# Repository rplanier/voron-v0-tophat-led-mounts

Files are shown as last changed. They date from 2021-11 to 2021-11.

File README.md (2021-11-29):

# Voron V0.1 Tophat LED Mounts

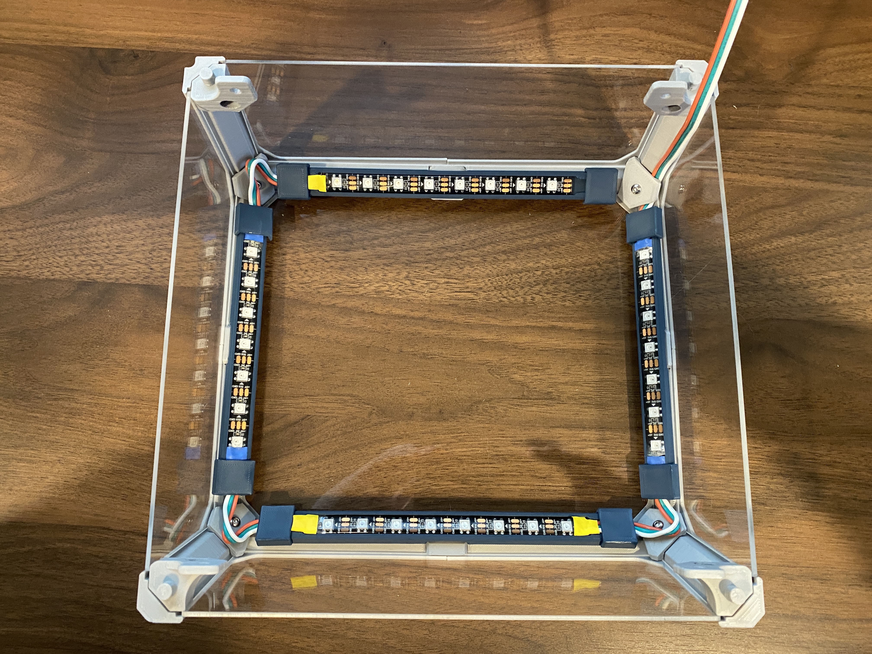
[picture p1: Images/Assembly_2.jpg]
Assembled Tophat


This mod for the Voron V0.1 adds four (4) LED mounting bars to the tophat and is designed to be minimumally intrusive and simple to build. It supports up to thirty (30) LEDs, which is the maximum officially supported using the BigTreeTech DCDC5V breakout power module. This guide assumes that you have a Voron V0.1 with a BigTreeTech SKR Mini E3 V2 controller board and the DCDC5V breakout power module (linked in the [BOM](#bill-of-materials) below.).

***Note:*** The LED mounting bars are too long to fit on a Voron V0 bed. However, the Fusion 360 CAD file has been included, and new mounting bars can easily be created by changing the user parameters.

## Table of Contents
- [Bill of Materials](#bill-of-materials)
- [Recommended Tools](#recommended-tools)
- [Printed Parts](#printed-parts)
- [Assembly Instructions](#assembly-instructions)
- [Klipper Configuration](#klipper-configuration)
- [Photos](#photos)
- [Contributors](#contributors)

## Bill of Materials

The following parts are required (unless otherwise denoted) to complete the assembly:

| Part | Quantity | Link | Notes |
| --- | :-: | --- | --- |
| BigTreeTech DCDC5V Power Module | 1 | https://www.biqu.equipment/products/bigtreetech-dcdc5v-v1-0-power-module-5v-for-skr-mini-e3-v1-2-skr-mini-e3-v3-0-32bit-control-board-rgb-light | Required to run up to 30 total LEDs, otherwise the SKR Mini E3 V2 only supports up to 8 LEDs. |
| WS2812B RGB IP65 5v LED Strip | 16.4 ft., 300 LEDs (OR) 3.2 f.t, 60 LEDs | https://amzn.to/3l4htHR | Channels in the mounting bars are designed to fit this exact 10mm-wide LED strip. Any LED strip you use should be 5 volts, 10mm wide, and approximately 16.5mm in length or less per LED diode. |
| 3-Pin 18 AWG PVC Copper Ribbon Wiring | 3+ ft. | https://amzn.to/3nSPr4d | 3-pin ribbon wiring is easier to work with for this mod, but any wiring will work. The reviews for the linked part suggest this wiring may actually be 20 AWG, but that is probably preferred anyway. |
| 1/4" Diameter Heat Shrink Tubing | 7 | https://amzn.to/3HMqvTM | Heat shrink tubing will protect the solder joints on the LED wiring pads (otherwise the pads may rip off during assembly). Cut 7 pieces to about 1/2" long each. |
| JST-XH 2.54mm 3-Pin Female Connector | 1 | https://amzn.to/30Vttoj | A JST-XH or similar 2.54mm connector is required to plug the LED strips into the Neopixel pins on the SKR Mini E3 V2 board. |
| Molex Micro-Fit 3.0 3-Pin Male/Female Connectors | 1 each | https://amzn.to/3FLt3zN | | **Optional**. To be added in-line within the printer chamber to allow for quick disconnects when removing the tophat for maintenance. |
| M3x10 Button Head Cap Screws | 8 | https://amzn.to/3HGdOd0 (OR) https://www.boltdepot.com/Product-Details.aspx?product=22819 | These will replace the 8x M3x6 screws used to bolt the tophat center clips to the tophat frame. |

## Recommended Tools

The following tools are recommended to complete the assembly:

| Tool | Link | Notes |
| --- | --- | --- |
| 3D Printer with >= 200mm Bed | | The largest part is about 185mm long, and you are encouraged to use a brim which further increases the length. ***No, the LED mounting bars will not fit on a Voron V0 bed.*** |
| Wire Strippers | https://amzn.to/3HNQ86u | For cutting and stripping wires between the LED strips. |
| Crimping Pliers | https://amzn.to/3cIcCry | For crimping JST-XH connector and other terminals. |
| Soldering Iron | https://amzn.to/3CNMZjv | You will need to solder 21 joints, plus maybe another 9 joints once you realize that once again you forgot to slide on the heat shrink tubing before soldering. |
| Tin Lead Rosin Core Solder Wire | https://amzn.to/30PILdR | |
| 2mm Hex Driver | | |

## Printed Parts

Each of the following parts should be printed in either ABS or ASA. ***Print each of the LED mounting bars with supports under the center of each bar where it will mount to the tophat center clip.***

| Part | Quantity | LED Angle | Supports Needed |
| --- | :-: | --- | --- |
| Front LED Bar | 1 | 15 degrees | Yes|
| Side LED Bar | 2 | 15 degrees | Yes |
| Back LED Bar | 1 | 5 degrees | Yes |
| End Clip | 8 | | No |

## Assembly Instructions

Reference the [photos](#photos) below during assembly for visual aid.

1. Print each of the [printed parts](#printed-parts). Test fit the end clips as described in Step 10 below.
2. Remove the existing M3x6 button head cap screws from the tophat center clips and install the front, back, and side LED mounting bars over the center clips using M3x10 button head cap screws. Each of the mounting bars is angled to better direct light toward the build plate. Ensure that the LED mounting bars are installed in the orientation that will direct light downward rather than upward.
3. Cut **2** strips of **7** LEDs for the front and back and **2** strips of **8** LEDs for the sides. I recommend leaving the full contact pad length on each end of a strip rather than cutting the contact pads in half. This means that for each 2 strips of LEDs you cut, you will throw away the LED diode between them because it won't have any contact pads. This will give you the greatest amount of surface area to ensure your soldering joints are strong.
4. Gently insert a seven **7**-LED strip and an **8**-LED strip into adjacent mounting bars to ensure that they will fit and measure the amount of 3-pin wire you will need between them. You will need somewhere around 3.5" of wire at each corner. Remove the strips from the mounting bars.
5. Cut off only the portion of IP65 protective plastic covering the contact pads on each end of the LED strips, except that you should not cut off the plastic covering the last set of contacts on the last LED strip since it will not be used. I have found the best way to do this is to peel away the covering from the LED strip by hand just enough to fully expose the contact pads and cut the covering with wire strippers.
6. Solder all the LED strips together with a strand of the measured 3-pin wire between each of them. ***Remember to add heat shrink tubing to your wires for each of your solder joints.***
7. Measure the length of wire needed to connect your first LED strip to the controller board and then cut and solder it to the first LED strip. If using a BigTreeTech SKR Mini E2 V2, crimp and add the JST-XH connector at the other end.
8. Slide the heat shrink tubing over the solder joints on each LED strip and apply heat to shrink them. Do not overheat or they will split and fall off.
9. Install each LED strip into its appropriate mounting bar by firmly pressing until it catches. You should not need to use the adhesive backing. Firmly press the wiring on each end of the LED strip into the mounting bar wiring channels.
10. Install the end clips on the ends of each mounting bar. The snap-fit connections are a bit oversized to ensure they strongly hold the wiring in place, so you may need to press firmly and/or twist the clips to install them properly.
11. Install the BigTreeTech DCDC5V power module onto the SKR Mini E3 V2 controller board. Be sure to move the appropriate jumper on the controller board to ensure it uses the power module rather than the on-board 5v controller for Neopixel/LED power (this is what allows you to use up to 30 LEDs rather than only 8). Consult the DCDC5V power module documentation for details.
12. Connect the JST-XH connector to the Neopixel port on the SKR Mini E3 V2.
13. Follow the [Klipper configuration](#klipper-configuration) instructions below for setting up the LEDs in the Klipper `printer.cfg` configuration file.

## Klipper Configuration

Add the following to `printer.cfg` in Klipper if using RGB LEDs:

```
###################################
# Neopixels / LEDs
###################################
[neopixel my_neopixel]
pin: PA8
chain_count: 30
color_order: GRB
initial_RED: 1
initial_GREEN: 1
initial_BLUE: 1
```

The LEDs can be changed by sending the command `SET_LED LED=my_neopixel RED={x} GREEN={x} BLUE={x}`, where `{x}` is a decimal value between 0 and 1. Consult the [Klipper documentation](https://www.klipper3d.org/Config_Reference.html#neopixel) for more information and configuration options.

## Photos

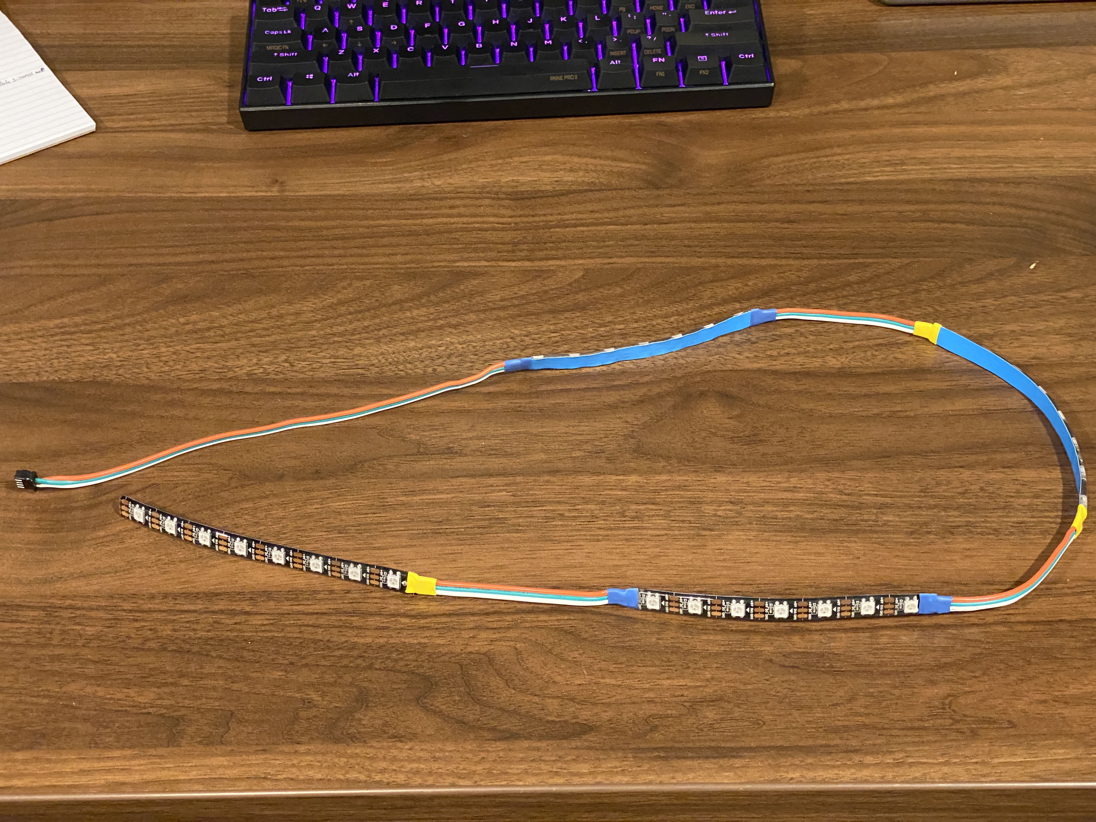
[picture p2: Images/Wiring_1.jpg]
Wiring 1

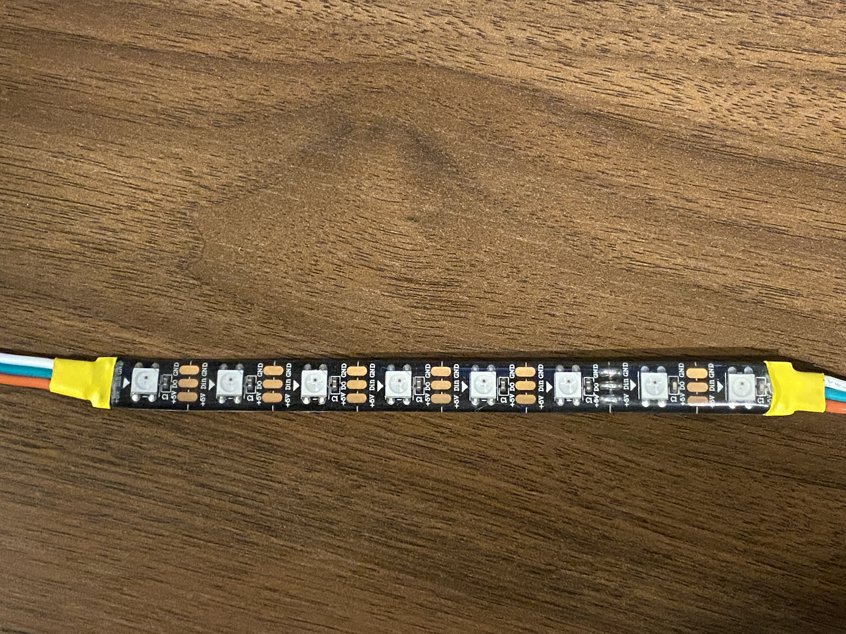
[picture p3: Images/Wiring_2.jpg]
Wiring

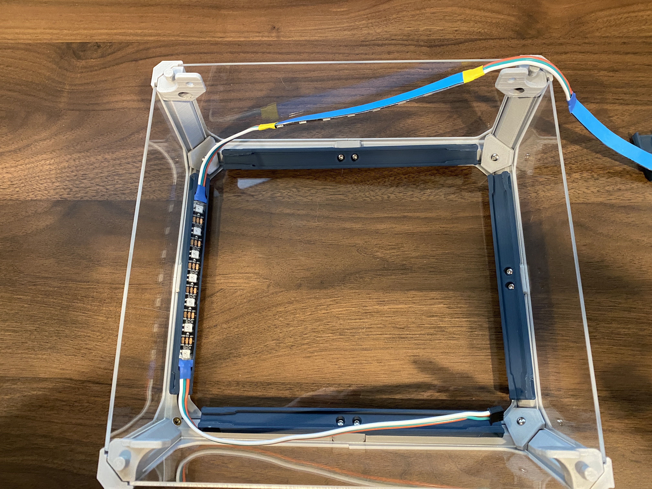
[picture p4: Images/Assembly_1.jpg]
Assembly 1

Assembly 2
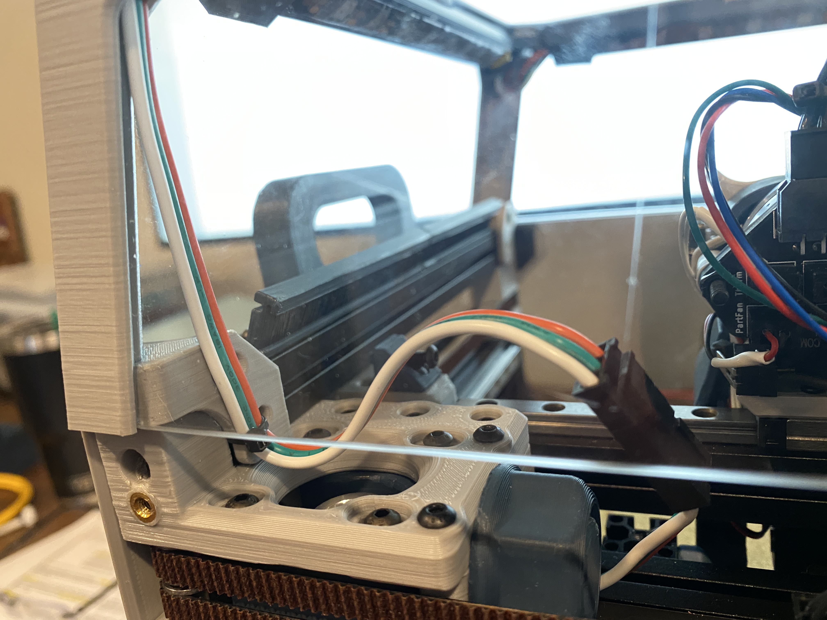
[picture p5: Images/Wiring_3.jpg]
Wiring 3

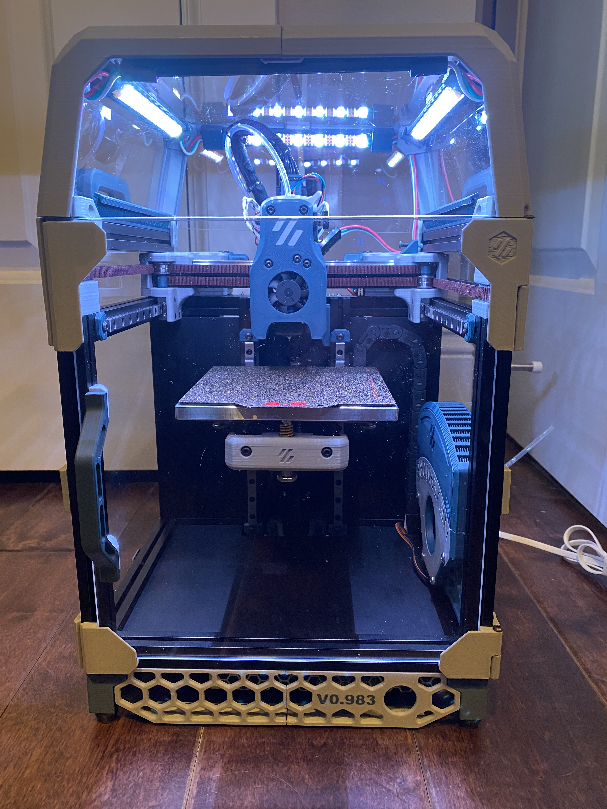
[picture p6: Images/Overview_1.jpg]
Overview 1

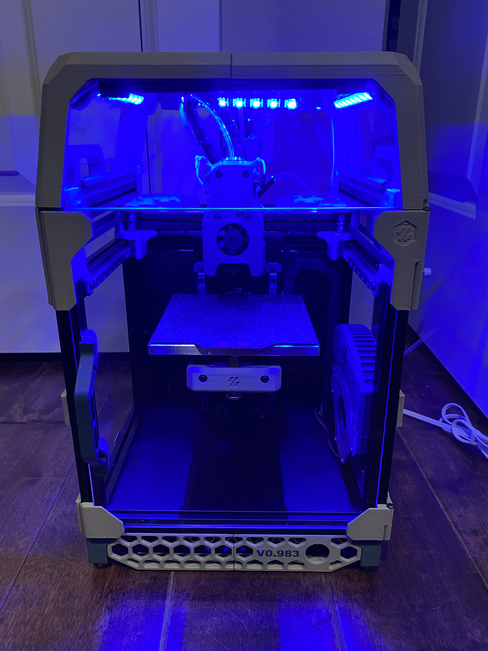
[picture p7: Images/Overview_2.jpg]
Overview 2

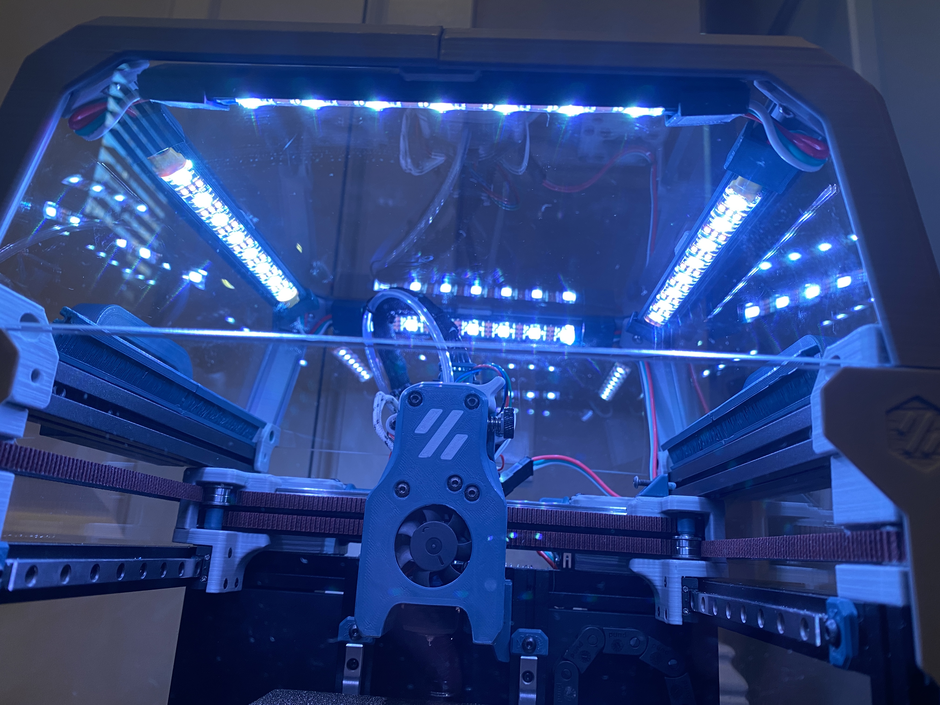
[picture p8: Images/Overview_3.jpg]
Overview 3

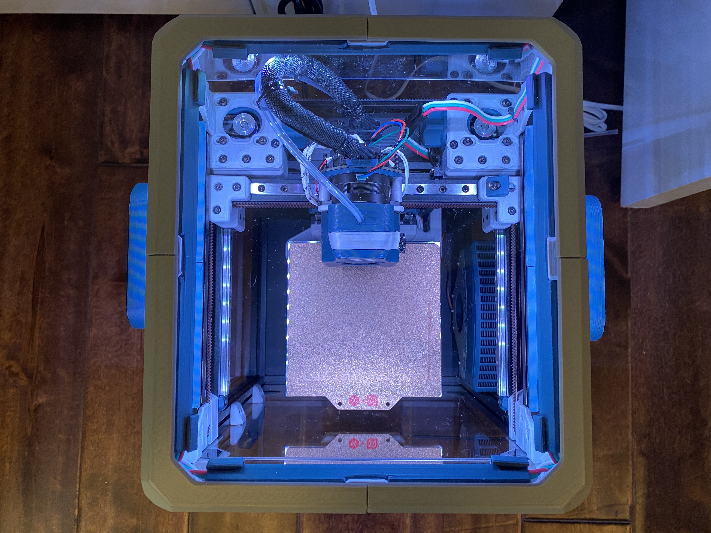
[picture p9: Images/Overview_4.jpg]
Overview 4


## Contributors
- Preston Lanier (**@rplanier#1125** on Voron Discord)

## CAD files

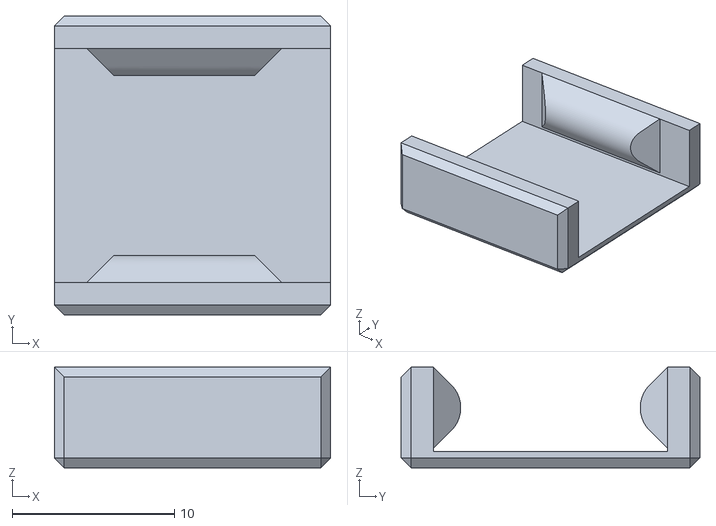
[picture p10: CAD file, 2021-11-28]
STL/End_Clip_8x.stl
17.0 x 18.4 x 6.20

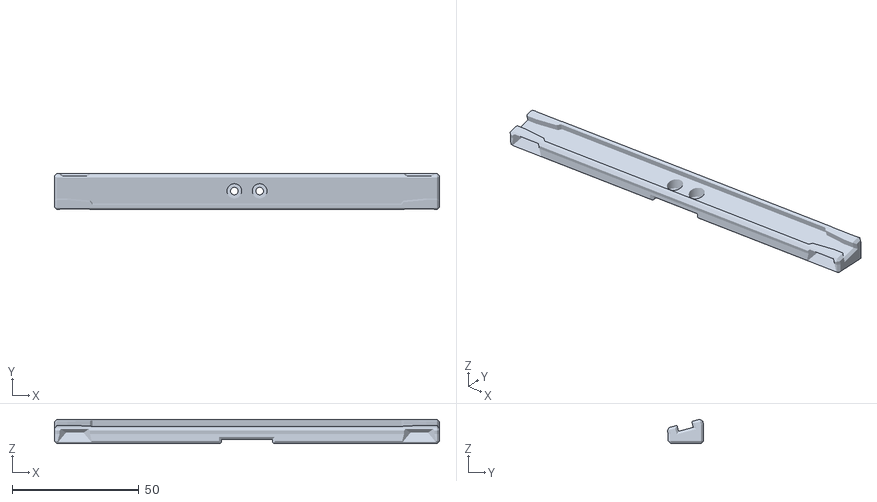
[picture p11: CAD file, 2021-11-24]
STL/Front_1x.stl
152.0 x 14.4 x 9.61

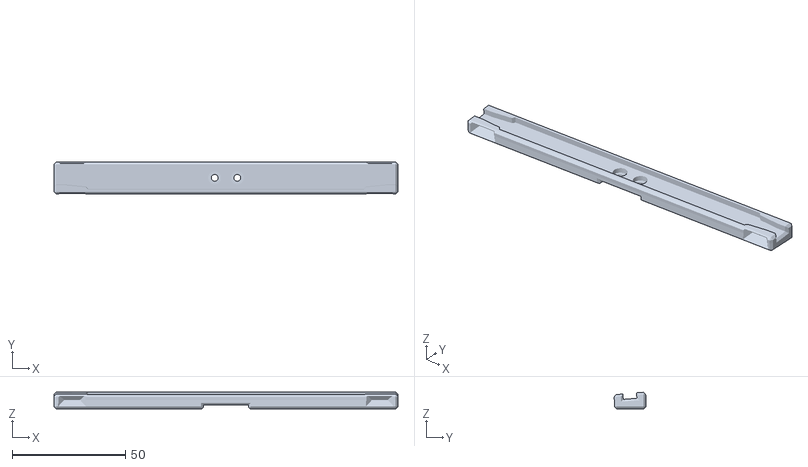
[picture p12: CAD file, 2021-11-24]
STL/Back_1x.stl
152.0 x 14.1 x 7.33

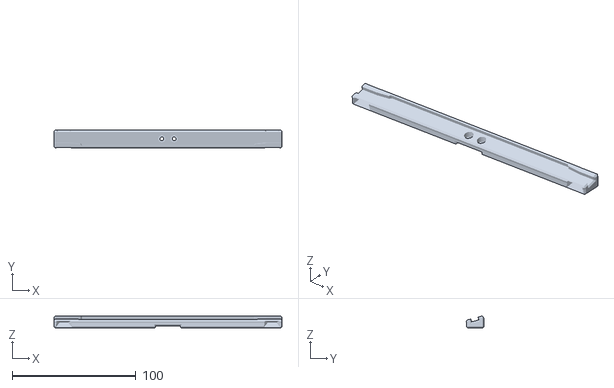
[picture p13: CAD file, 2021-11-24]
STL/Side_2x.stl
184.0 x 14.4 x 9.61

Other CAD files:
CAD/V0 Tophat LED Mounts.f3d

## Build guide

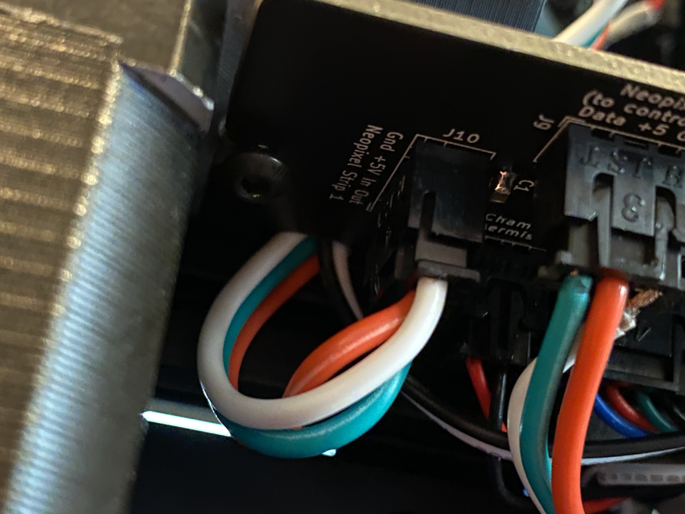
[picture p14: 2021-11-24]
Images/Wiring_4.jpg

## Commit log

2021-11-24 Initial commit of first design
    [Back_1x.stl, End_Clip_8x.stl, Front_1x.stl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]
2021-11-25 Fix BOM anchor tag typo
2021-11-28 Shorten and round over snap fit extrusion
    [End_Clip_8x.stl]
